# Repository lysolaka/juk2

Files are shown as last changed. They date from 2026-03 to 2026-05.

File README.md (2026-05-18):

# JUK2

JUK2 is a CNC plotter firmware for the ESP32-S3 on a custom PCB and plotter frame.

JUK2 is the successor of JUK - a private, messy and ugly project. The project's second version is supposed to be everything the first one was not able to be.

See the file `REFERENCE.md` for usage information.

# Hardware

The custom design can be found under the `juk-pcb` directory. It also has a schematic and a STEP model available for those, who don't have KiCad installed.

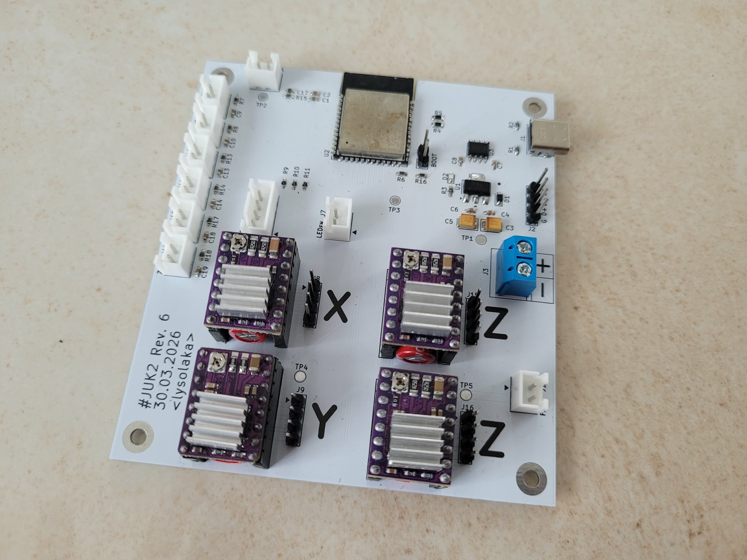
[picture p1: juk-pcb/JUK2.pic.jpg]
juk2pcb


The machine operates in Cartesian coordinates using four motors: one for X and Y axes each, and two for the Z axis. The X axis is realized as a moving table, the Y axis is being moved up and down by the Z axis. The X and Y assemblies operate using a belt pulley, the Z axis moves the Y axis assembly using trapezoidal screws from both ends of the axis (hence the need for two motors).

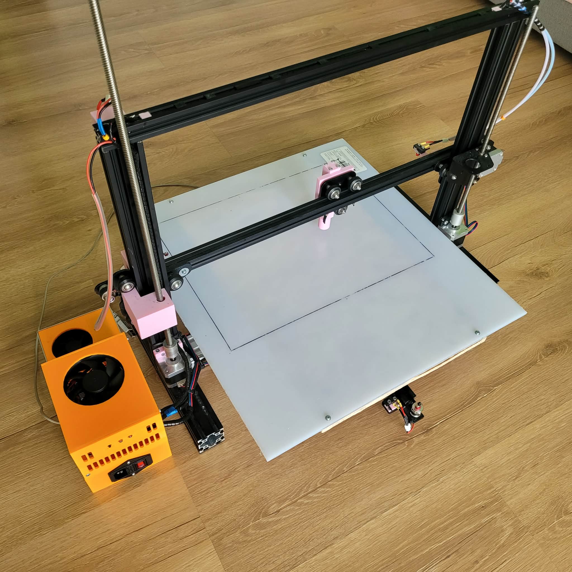
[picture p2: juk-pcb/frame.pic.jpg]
juk2frame


# Software

Just like the first edition of JUK, the entire software stack is developed using Rust. This time the project is split into crates in a single workspace. The structure is as follows:
- `juk-cmd`: command parsing and wire protocol library
- `juk-com`: a communication library implementing text and binary interfaces
- `juk-firmware`: the main firmware executable
- `juk-interp`: movement interpolators library
- `juk-led`: a simple library to use an RGB LED using PWM
- `juk-motion`: motion profiles library

## Toolchain

Building this project requires the Xtensa Rust Toolchain, detailed installation instructions can be found [here](https://docs.espressif.com/projects/rust/book/getting-started/toolchain.html). Additionaly the [espflash](https://github.com/esp-rs/espflash/tree/main/espflash) utility is needed to flash the program onto the board.

# License

All code and design files in this repository are licensed under the GPL-3 license.

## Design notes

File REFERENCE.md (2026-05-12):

# JUK2 - Reference

# Configuration Options

## Summary

| Option | Data Type | Values | Default Value |
|---|---|---|---|
| `accel`  | `f32` | \[`0.0`, `100000.0`\] | *TODO* |
| `frame`  | `enum` | `rel`, `abs` | `rel` |
| `led` | `u32` | \[`000000`, `ffffff`\]  | `00ff00` |
| `limits` | `[bool; 6]` | key is read-only | *undefined* |
| `mmpsX`  | `f32` | \(`0.0`, `1.0`\] | `0.0125625` |
| `mmpsY`  | `f32` | \(`0.0`, `1.0`\] | `0.0125625` |
| `mmpsZ`  | `f32` | \(`0.0`, `1.0`\] | *TODO* |
| `posX` | `i32` | \[`0`, `50000`\] | `0` |
| `posY` | `i32` | \[`0`, `50000`\] | `0` |
| `posZ` | `i32` | \[`0`, `50000`\] | `0` |
| `unit` | `enum` | `steps`, `mm` | `steps` |
| `vel` | `f32` | \[`0.0`, `50000.0`\] | *TODO* |

## Description

#### `accel` - Default Acceleration

Data type: `f32`
Value range: \[`0.0`, `100000.0`\]
Default value: *TODO*

Default acceleration value in `steps / s^2` used when the acceleration motion parameter is ommited.

Example:
```
set accel=12000.0
```

#### `frame` - Displacement Reference Frame

Data type: `enum`
Variants: `rel`, `abs`
Default value: `rel`

Reference frame to use when moving. `rel` means relative to the current position, `abs` - relative to the origin of the \[`posX`, `posY`, `posZ`\] vector.

Example:
```
set frame=abs
```

#### `led` - RGB LED Colour

Data type: `u32`
Value range: \[`000000`, `ffffff`\]
Default value: `00ff00`

RGB8 value in HTML notation.

Example:
```
set led=ff00ff
```

#### `limits` - Limit Switch Status

Data type: `[bool; 6]`
Default value: *undefined*

Limit switch status for each axis and each direction. The data type doesn't matter - the software will display the output in a friendly format.

This configuration key is read-only and cannot be used with the `set` command.

Example:
```
get limits
```

#### `mmps{X,Y,Z}` - Millimeters per Step Coefficient

Data type: `f32`
Value range: \(`0.0`, `1.0`\]
Default value:
- `mmps{X,Y}`: `0.0125625`
- `mmpsZ`: *TODO*

Millimeters per step coefficient for an axis. To make a move when the value of `unit` is `mm`, the displacement value is divided by its axis `mmps` value and rounded to the nearest integer.

Example:
```
set mmpsX=0.02
set mmpsY=0.0125
set mmpsZ=0.005
```

#### `pos{X,Y,Z}` - Current Position

Data type: `u32`
Value range: \[`0`, `50000`\]
Default value: `0`

Current position of the end-effector in the unit of steps. Each axis' value is set to 0 after homing that axis. Changing this value does not move the end-effector, it only changes the reference frame.

Example:
```
set posX=100
set posY=43
set posZ=0
```

#### `unit` - Displacement Units

Data type: `enum`
Variants: `steps`, `mm`
Default value: `steps`

Units to use for the displacement values. `steps` is in the unit of motor steps, `mm` is for millimeters.

Example:
```
set unit=mm
```

#### `vel` - Default Velocity

Data type: `f32`
Value range: \[`0.0`, `50000.0`\]
Default value: *TODO*

Default velocity value in `steps / s` used when the velocity motion parameter is ommited.

Example:
```
set vel=5000.0
```

# Interface

## Interface Modes

The interface can be in one of two states: text or binary. After reset the state is set to text, the user may communicate with the machine using a command line interface. Binary mode is used for communicating with a PC using messages in a binary format. To switch between the modes the user has to press `CTRL + Space` once or twice, depending on the current state of the input buffer. The user is also notified about the switch by a message on the terminal when said switch happens. The external RGB indicator colour shows the current mode: green means text mode, magenta - binary mode.

## Keybindings

While the interface is in text mode, the following key combinations are recognised:
- `?`: Displays help based on the current command, if the command name is not entered, displays the command list
- `CTRL + X`: Cancels the current movement and flushes the execution queue
- `CTRL + C`: Cancels the current input at the command line
- `CTRL + D`: If the command line is empty, issues a software reset
- `CTRL + Space`: Switch between text mode and binary mode
- `CTRL + G`: Easter egg

# Command Reference

## Arguments

Some commands have key-value arguments, they are given as:
```
<key>=<value>
```
where key names are strings. Values are parsed on a per-key basis: each key has their value requirements listed in its description.

## Displacement Arguments

Allowed values for displacement arguments depend on the current reference frame (config: `frame`) and the current unit (config: `unit`).

That is:
- `frame` = `rel`, `unit` = `steps`:
    - Data type: integer
    - Range: \[-50000, 50000\]

- `frame` = `rel`, `unit` = `mm`:
    - Data type: floating-point
    - Range: \[-500, 500\]

- `frame` = `abs`, `unit` = `steps`:
    - Data type: integer
    - Range: \[0, 50000\]

- `frame` = `abs`, `unit` = `mm`:
    - Data type: floating-point
    - Range: \[0, 5000\]

## Motion Arguments

Allowed values for acceleration and velocity arguments depend on the current unit (config: `unit`).

- `unit` = `steps`
    - Data type: floating-point
    - Range: 
        - acceleration: \[0, 100000\]
        - velocity: \[0, 50000\]

- `unit` = `mm`
    - Data type: floating-point
    - Range: the values must be non-negative and after conversion to steps, must fit into the range for `unit` = `steps`.

The acceleration is given as unit per second squared, velocity as unit per second.

## Argument Relations

If a command has required arguments, their description has an argument relation statement.

Let an imaginary command have argument keys:
- `foo`
- `bar`
- `baz`

The following list shows relation statements and their meaning (if a key is missing it is optional)

- `foo`, `bar`, `baz` are required:
```
* ( foo bar baz )
```

- At least one of `foo`, `bar`, `baz`:
```
|| ( foo bar baz )
```

- Exactly one of `foo`, `bar`, `baz`:
```
^^ ( foo bar baz )
```

## Commands List

#### `move` - Move in a Line

Examples:
```
move x=120 y=-400
move x=40.0 y=60.0 z=0.0
move x=1250 a=12000 v=8000
move x=-100.0 z=50.0 a=0
```

**Keys:**
- `x`: X axis displacement.
- `y`: Y axis displacement.
- `z`: Z axis displacement.
- `a`: Movement acceleration.
- `v`: Movement velocity.

**Relation:**
```
|| ( x y z )
```

#### `arc` - Move in an Arc

Examples:
```
arc x=-100 y=100 r=100 dir=pos
arc x=20.0 y=10.0 r=40.0 dir=neg
arc x=120 y=80 r=240 a=0 v=50
arc x=-10.0 y=-10.0 r=10.0 dir=neg a=500.0 v=100.0
```

**Keys:**
- `x`: X axis displacement.
- `y`: Y axis displacement.
- `z`: Z axis displacement. The arc is done in the XY plane. Use this to achieve helical motion.
- `r`: Arc radius. Adheres to the same rules as displacement, but must not be negative.
- `dir`: direction of the arc. `pos` means the direction where the angle of the radius vector increases, `neg` - where the angle decreases. Allowed values: `pos`, `neg`. Default is: `pos`
- `a`: Movement acceleration.
- `v`: Movement velocity.

**Relation:**
```
* ( x y r )
```

#### `home` - Perform Homing

Examples:
```
home
home axis=x
home axis=zy
home axis=xyz
```

**Keys:**
- `axis`: the axis (axes) to perform homing on. The only axes are `x`, `y`, `z`, so any combination of these three may be used. Default is: `xyz`.

#### `set` - Alter the configuration

Examples:
```
set unit=mm
set mmpsX=0.0125 posX=0 posY=500
```

**Keys:**

*see the configuration reference for the list of keys and their description*

**Relation:**
```
|| ( <keys> )
```

#### `get` - View the configuration

Examples:
```
get posX
get frame
get status
```

This commands functions differently than the others, namely the keys do not accept a value. This means that the following is an error:
```
get pos=loremipsum
```

**Keys:**

*see the configuration reference for the list of keys and their description*

Additionally the following keys are available:
- `pos`: absolute position of every axis in steps
- `mmps`: millimeters per step coefficient for every axis
- `status`: combined `pos`, `frame`, `unit` and limit switch information
- `version`: version information
- `license`: license information

**Relation:**
```
^^ ( <keys> )
```

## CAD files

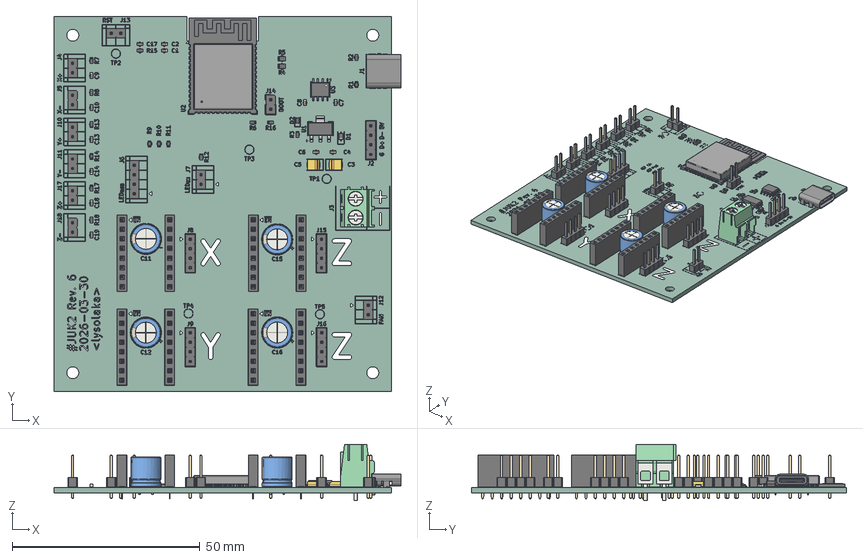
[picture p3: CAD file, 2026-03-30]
juk-pcb/JUK2.step
92.5 x 100.0 x 15.0 mm
PinHeader_1x02_P2.54mm_Vertical x 10
PinHeader_1x04_P2.54mm_Vertical x 6
R_0603_1608Metric x 16
C_0603_1608Metric x 13
PinSocket_1x08_P2.54mm_Vertical x 8
CP_Radial_D8.0mm_P3.50mm x 4
ESP32-S3-WROOM-1
D_SOD-323
TerminalBlock_Phoenix_PT-1,5-2-5.0-H_1x02_P5.00mm_Horizontal
R_0805_2012Metric x 2
JEITA_SOIC-8_3.9x4.9mm_P1.27mm
SOT-223
D_0603_1608Metric
CP_EIA-3528-15_AVX-H x 2
USB_C_Receptacle_GCT_USB4085
JUK2_silkscreen
JUK2_PCB

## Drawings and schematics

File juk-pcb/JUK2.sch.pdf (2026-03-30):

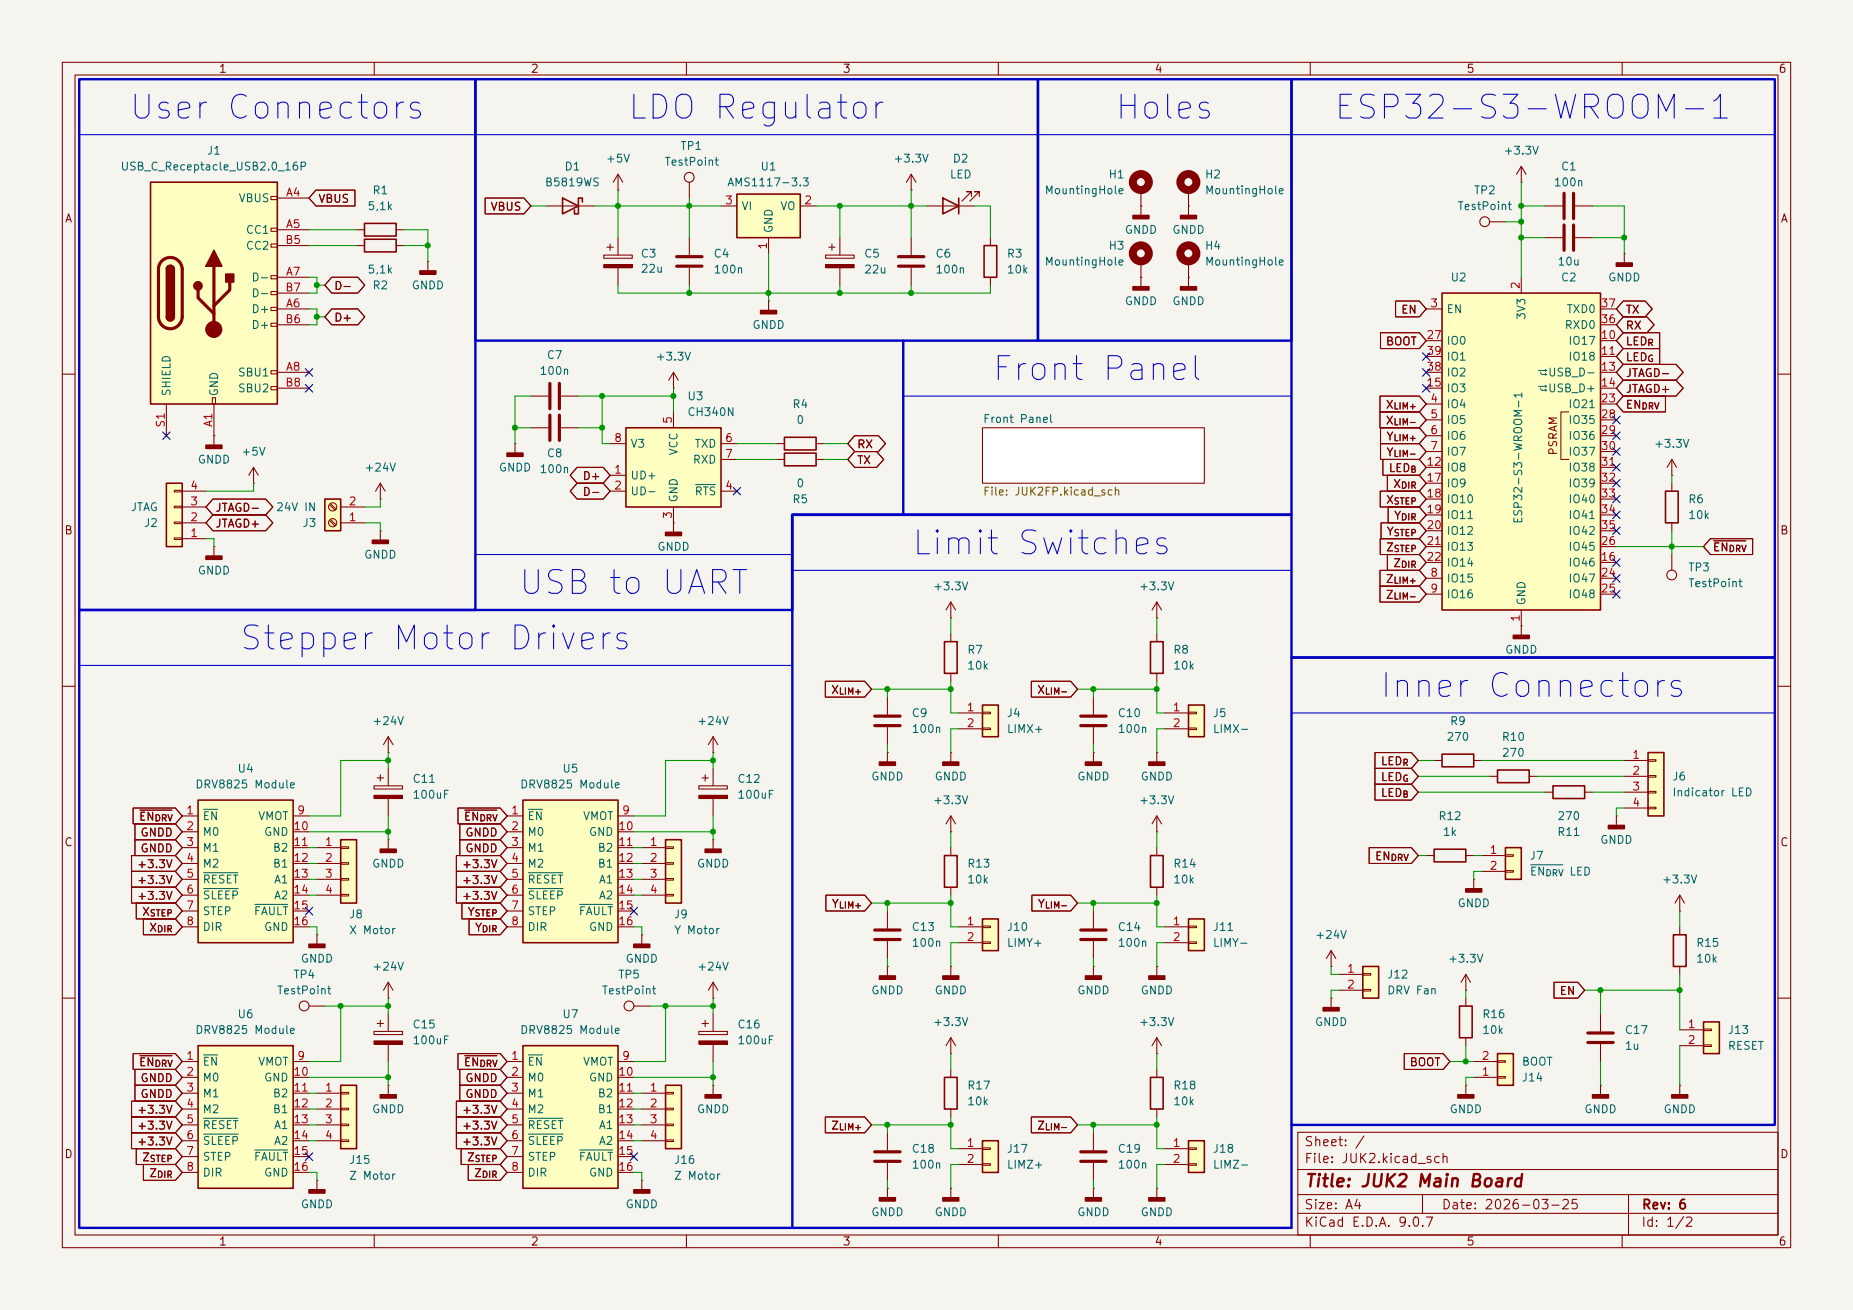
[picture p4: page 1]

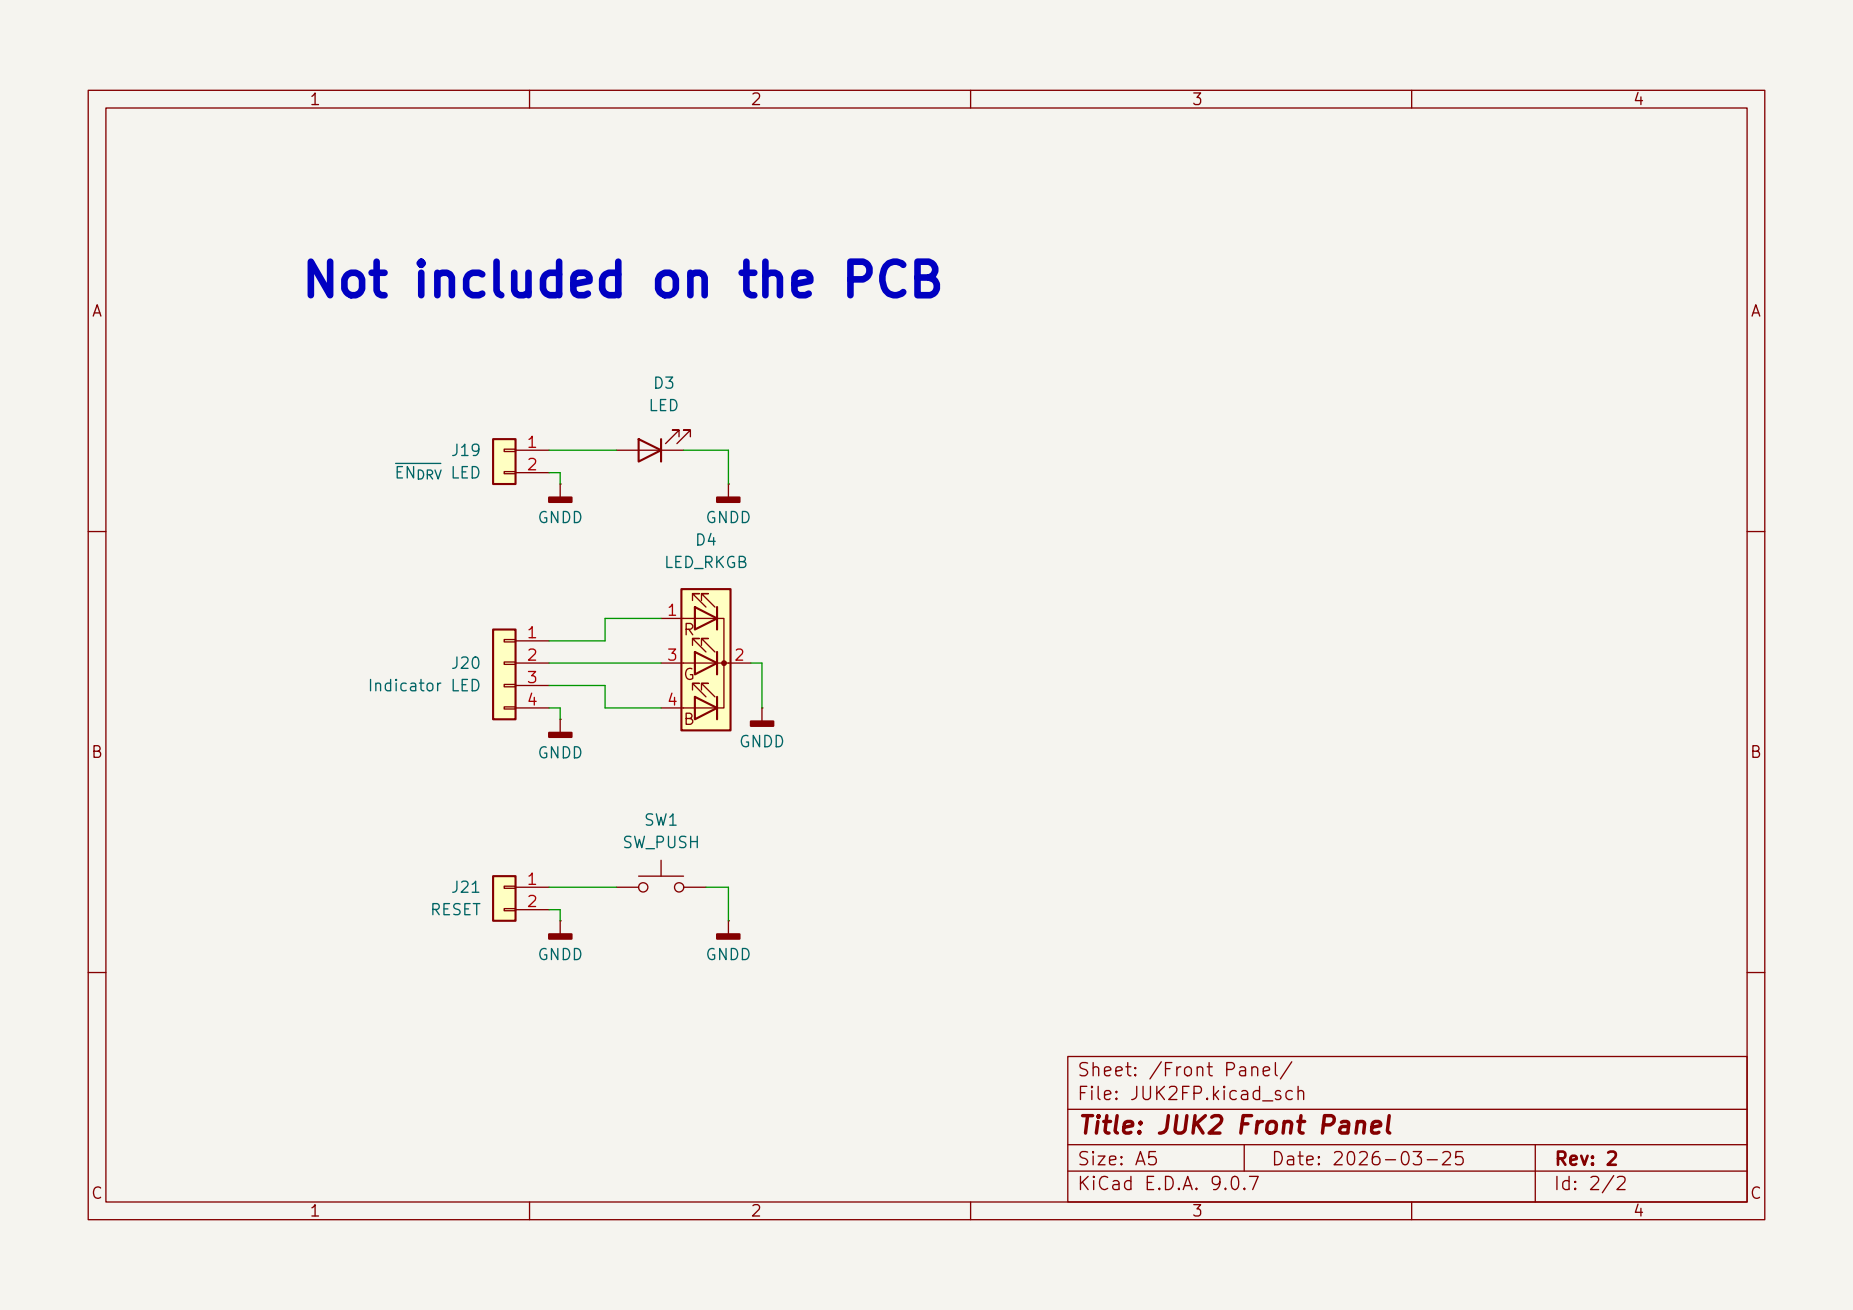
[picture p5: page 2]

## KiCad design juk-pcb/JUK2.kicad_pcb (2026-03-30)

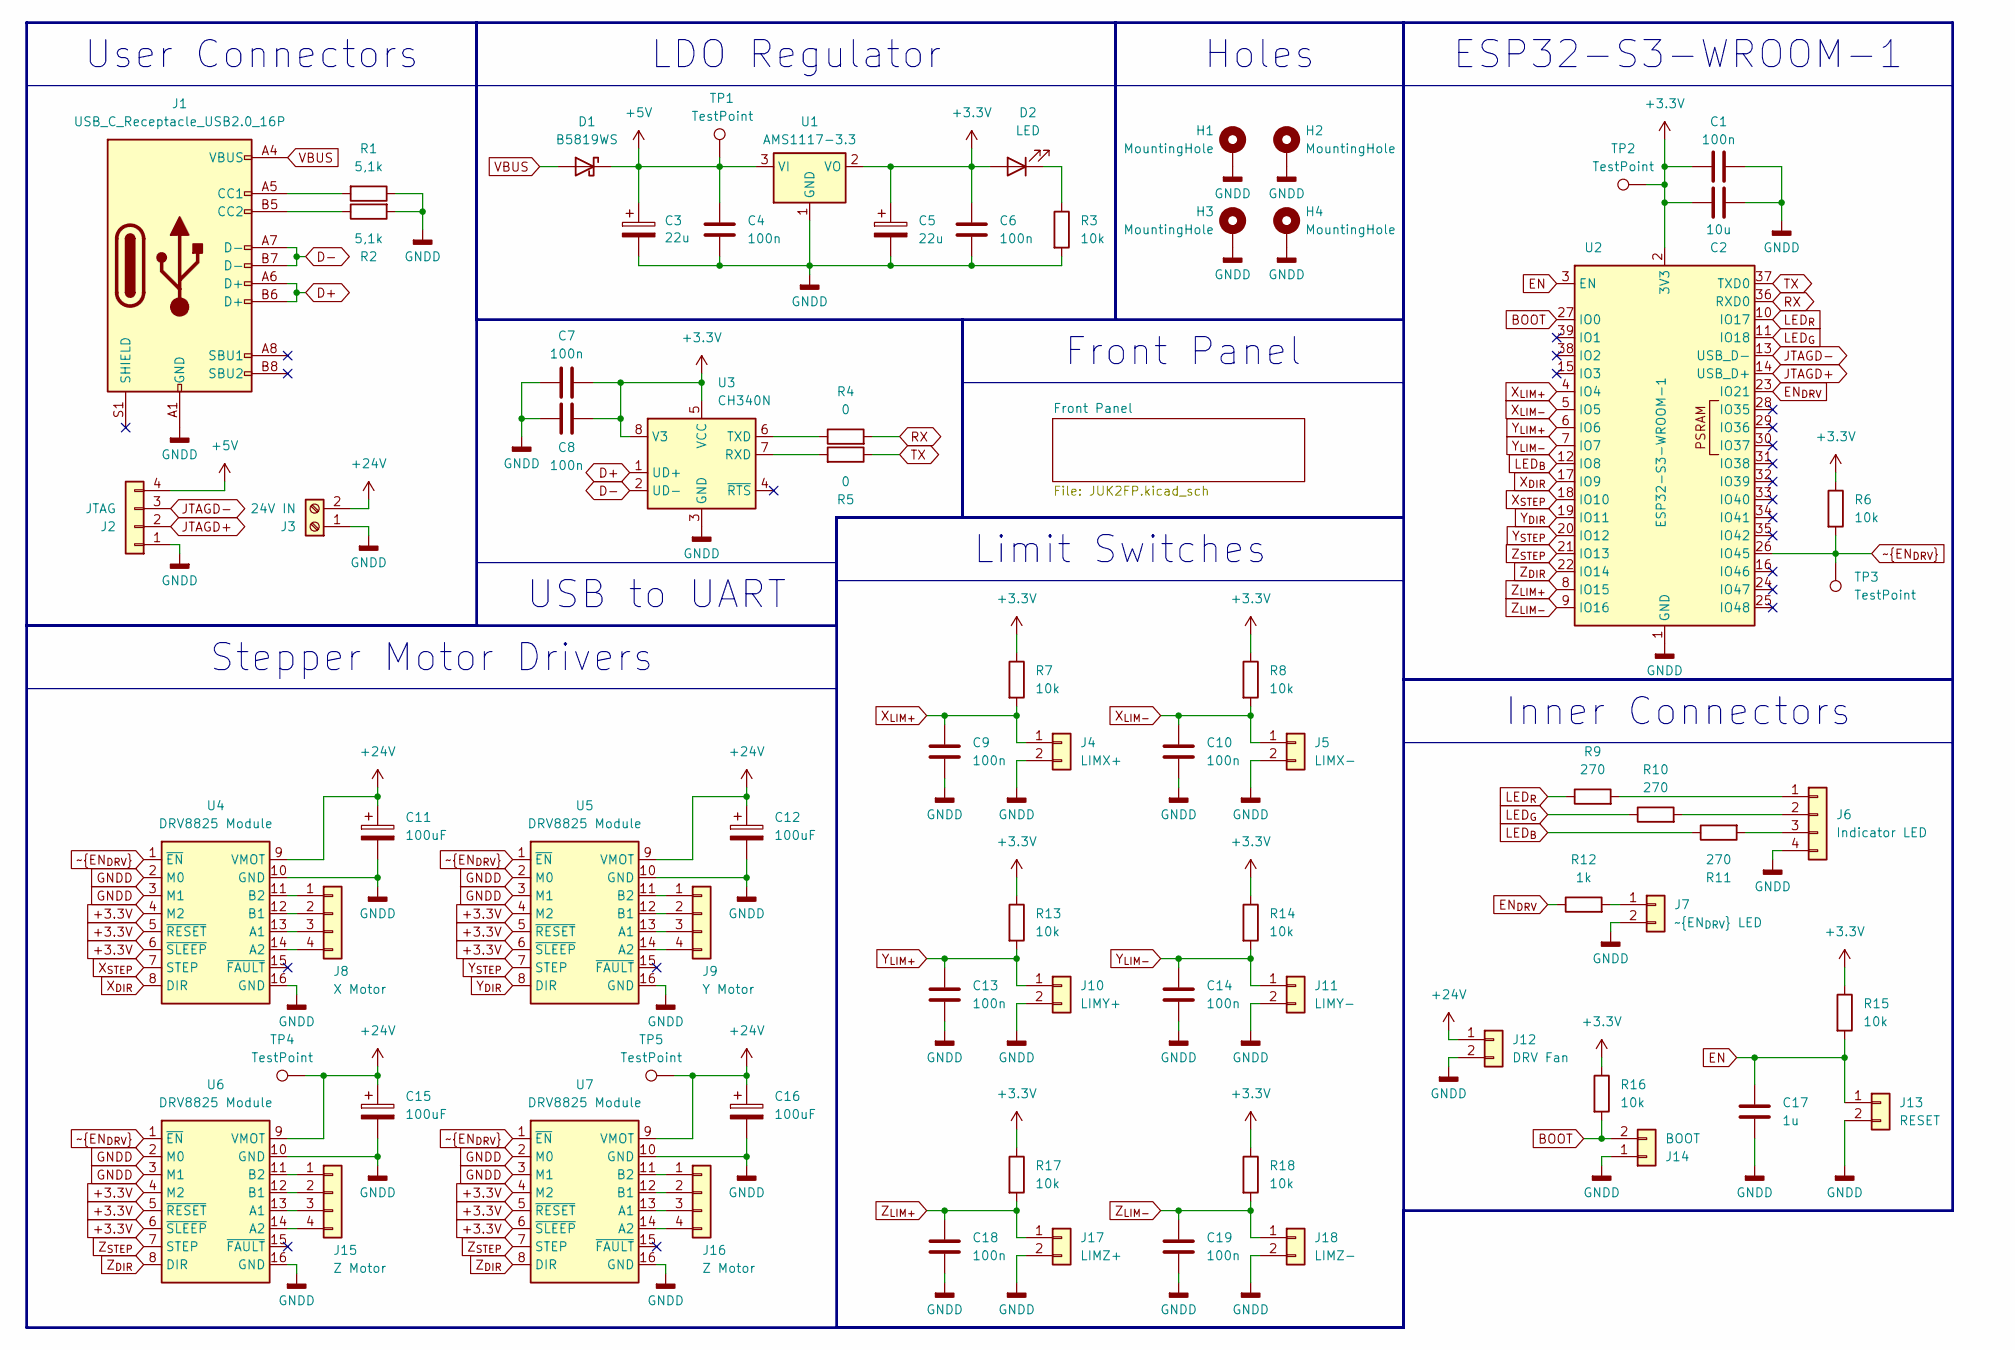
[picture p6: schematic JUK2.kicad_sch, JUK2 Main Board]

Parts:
C1, C4, C6, C7, C8, C9, C10, C13, C14, C18, C19: 100n; C_0603_1608Metric_Pad1.08x0.95mm_HandSolder
C2: 10u; C_0603_1608Metric_Pad1.08x0.95mm_HandSolder
C3, C5: 22u; CP_EIA-3528-15_AVX-H_HandSolder
C11, C12, C15, C16: 100uF; CP_Radial_D8.0mm_P3.50mm
C17: 1u; C_0603_1608Metric_Pad1.08x0.95mm_HandSolder
D1: B5819WS; D_SOD-323_HandSoldering
D2: LED; D_0603_1608Metric_Pad1.05x0.95mm_HandSolder
H1, H2, H3, H4: MountingHole; MountingHole_3.2mm_M3_Pad
J1: USB_C_Receptacle_USB2.0_16P; USB_C_GCT_USB4085
J2: JTAG; JTAGConnector
J3: 24V IN; TerminalBlock
J4: LIMX+; 2PinConnector
J5: LIMX-; 2PinConnector
J6: Indicator LED; 4PinConnector
J7: ~{EN_{DRV}} LED; 2PinConnector
J8: X Motor; MotorConnector
J9: Y Motor; MotorConnector
J10: LIMY+; 2PinConnector
J11: LIMY-; 2PinConnector
J12: DRV Fan; 2PinConnector
J13: RESET; 2PinConnector
J14: BOOT; PinHeader_1x02_P2.54mm_Vertical
J15, J16: Z Motor; MotorConnector
J17: LIMZ+; 2PinConnector
J18: LIMZ-; 2PinConnector
R1, R2: 5,1k; R_0603_1608Metric_Pad0.98x0.95mm_HandSolder
R3, R6, R7, R8, R13, R14, R15, R16, R17, R18: 10k; R_0603_1608Metric_Pad0.98x0.95mm_HandSolder
R4, R5: 0; R_0805_2012Metric_Pad1.20x1.40mm_HandSolder
R9, R10, R11: 270; R_0603_1608Metric_Pad0.98x0.95mm_HandSolder
R12: 1k; R_0603_1608Metric_Pad0.98x0.95mm_HandSolder
TP1, TP2, TP3, TP4, TP5: TestPoint; TestPoint_Pad_D2.0mm
U1: AMS1117-3.3; SOT-223-3_TabPin2
U2: ESP32-S3-WROOM-1
U3: CH340N; JEITA_SOIC-8_3.9x4.9mm_P1.27mm
U4, U5, U6, U7: DRV8825 Module; DRV8825_Module

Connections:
+3.3V: C1.1, C2.2, C5.1, C6.1, C7.2, C8.2, D2.2 (A), R6.1, R7.1, R8.1, R13.1, R14.1, R15.1, R16.1, R17.1, R18.1, TP2.1, U1.2 (VO), U2.2 (3V3), U3.5 (VCC), U3.8 (V3), U4.4 (M2), U4.5 (~RESET), U4.6 (~SLEEP), U5.4 (M2), U5.5 (~RESET), U5.6 (~SLEEP), U6.4 (M2), U6.5 (~RESET), U6.6 (~SLEEP), U7.4 (M2), U7.5 (~RESET), U7.6 (~SLEEP)
+5V: C3.1, C4.1, D1.1 (K), J2.4, TP1.1, U1.3 (VI)
+24V: C11.1, C12.1, C15.1, C16.1, J3.2, J12.1, TP4.1, TP5.1, U4.9 (VMOT), U5.9 (VMOT), U6.9 (VMOT), U7.9 (VMOT)
BOOT: J14.2, R16.2, U2.27 (IO0)
D+: J1.A6 (D+), J1.B6 (D+), U3.1 (UD+)
D-: J1.A7 (D-), J1.B7 (D-), U3.2 (UD-)
EN: C17.1, J13.1, R15.2, U2.3 (EN)
EN_{DRV}: R12.1, U2.23 (IO21)
GNDD: C1.2, C2.1, C3.2, C4.2, C5.2, C6.2, C7.1, C8.1, C9.2, C10.2, C11.2, C12.2, C13.2, C14.2, C15.2, C16.2, C17.2, C18.2, C19.2, H1.1, H2.1, H3.1, H4.1, J1.A1 (GND), J1.A12 (GND), J1.B1 (GND), J1.B12 (GND), J2.1, J3.1, J4.2, J5.2, J6.4, J7.2, J10.2, J11.2, J12.2, J13.2, J14.1, J17.2, J18.2, R1.1, R2.2, R3.2, U1.1 (GND), U2.1 (GND), U2.40 (GND), U2.41 (GND), U3.3 (GND), U4.2 (M0), U4.3 (M1), U4.10 (GND), U4.16 (GND), U5.2 (M0), U5.3 (M1), U5.10 (GND), U5.16 (GND), U6.2 (M0), U6.3 (M1), U6.10 (GND), U6.16 (GND), U7.2 (M0), U7.3 (M1), U7.10 (GND), U7.16 (GND)
JTAGD+: J2.2, U2.14 (USB_D+)
JTAGD-: J2.3, U2.13 (USB_D-)
LED_{B}: R11.1, U2.12 (IO8)
LED_{G}: R10.1, U2.11 (IO18)
LED_{R}: R9.1, U2.10 (IO17)
unnamed: D2.1 (K), R3.1
unnamed: J1.A5 (CC1), R1.2
unnamed: J1.B5 (CC2), R2.1
unnamed: J6.1, R9.2
unnamed: J6.2, R10.2
unnamed: J6.3, R11.2
unnamed: J7.1, R12.2
unnamed: J8.1, U4.11 (B2)
unnamed: J8.2, U4.12 (B1)
unnamed: J8.3, U4.13 (A1)
unnamed: J8.4, U4.14 (A2)
unnamed: J9.1, U5.11 (B2)
unnamed: J9.2, U5.12 (B1)
unnamed: J9.3, U5.13 (A1)
unnamed: J9.4, U5.14 (A2)
unnamed: J15.1, U6.11 (B2)
unnamed: J15.2, U6.12 (B1)
unnamed: J15.3, U6.13 (A1)
unnamed: J15.4, U6.14 (A2)
unnamed: J16.1, U7.11 (B2)
unnamed: J16.2, U7.12 (B1)
unnamed: J16.3, U7.13 (A1)
unnamed: J16.4, U7.14 (A2)
unnamed: R5.2, U3.7 (RXD)
unnamed: R4.1, U3.6 (TXD)
RX: R4.2, U2.36 (RXD0)
TX: R5.1, U2.37 (TXD0)
VBUS: D1.2 (A), J1.A4 (VBUS), J1.A9 (VBUS), J1.B4 (VBUS), J1.B9 (VBUS)
X_{DIR}: U2.17 (IO9), U4.8 (DIR)
X_{LIM+}: C9.1, J4.1, R7.2, U2.4 (IO4)
X_{LIM-}: C10.1, J5.1, R8.2, U2.5 (IO5)
X_{STEP}: U2.18 (IO10), U4.7 (STEP)
Y_{DIR}: U2.19 (IO11), U5.8 (DIR)
Y_{LIM+}: C13.1, J10.1, R13.2, U2.6 (IO6)
Y_{LIM-}: C14.1, J11.1, R14.2, U2.7 (IO7)
Y_{STEP}: U2.20 (IO12), U5.7 (STEP)
Z_{DIR}: U2.22 (IO14), U6.8 (DIR), U7.8 (DIR)
Z_{LIM+}: C18.1, J17.1, R17.2, U2.8 (IO15)
Z_{LIM-}: C19.1, J18.1, R18.2, U2.9 (IO16)
Z_{STEP}: U2.21 (IO13), U6.7 (STEP), U7.7 (STEP)
~EN_{DRV}: R6.2, TP3.1, U2.26 (IO45), U4.1 (~EN), U5.1 (~EN), U6.1 (~EN), U7.1 (~EN)

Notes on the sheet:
ESP32-S3-WROOM-1
Limit Switches
Front Panel
LDO Regulator
Holes
Inner Connectors
USB to UART
Stepper Motor Drivers
User Connectors

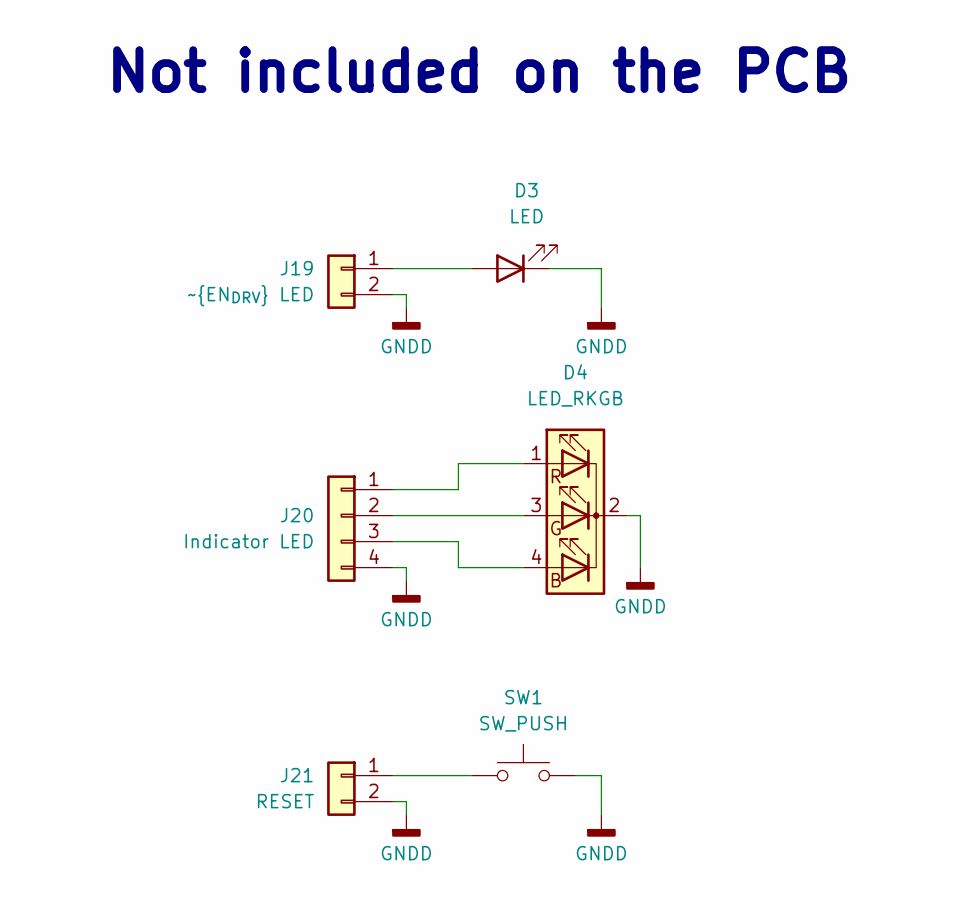
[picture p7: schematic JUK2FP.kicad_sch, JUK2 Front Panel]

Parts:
D3: LED; LED_D5.0mm
D4: LED_RKGB; LED_D5.0mm-4_RKGB
J19: ~{EN_{DRV}} LED; 2PinConnector
J20: Indicator LED; 4PinConnector
J21: RESET; 2PinConnector
SW1: SW_PUSH; SW_PUSH_6mm_H13mm

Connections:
unnamed: D3.1 (K), D4.2 (K), J19.2, J20.4, J21.2, SW1.2
unnamed: D3.2 (A), J19.1
unnamed: D4.1 (RA), J20.1
unnamed: D4.3 (GA), J20.2
unnamed: D4.4 (BA), J20.3
unnamed: J21.1, SW1.1

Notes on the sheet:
Not included on the PCB

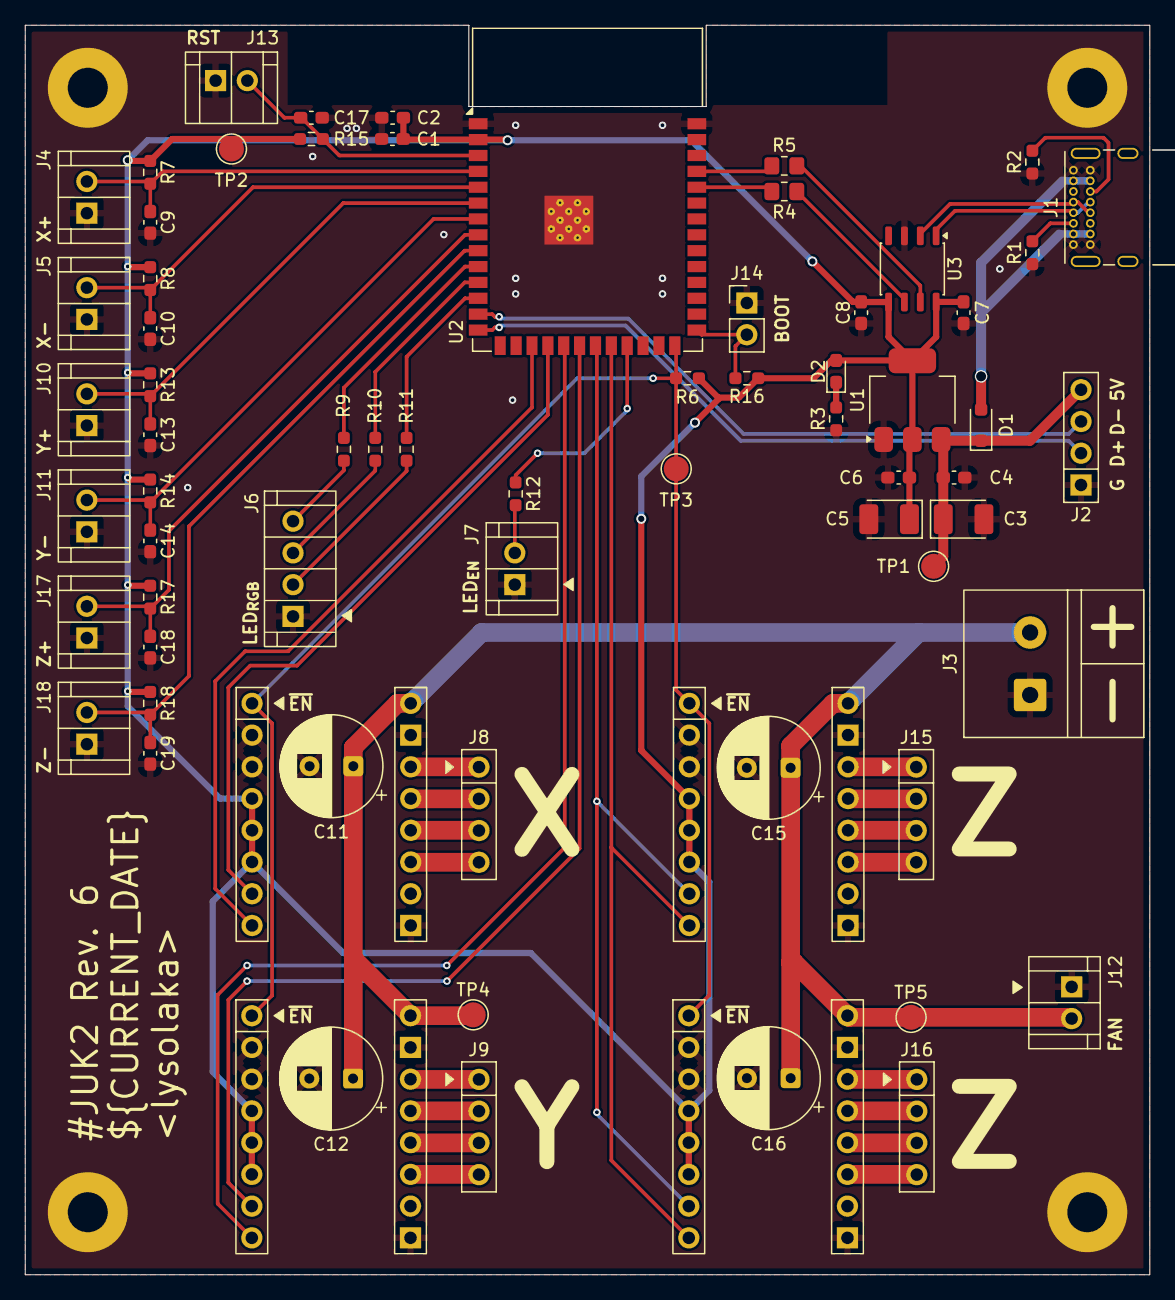
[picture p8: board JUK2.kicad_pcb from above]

Board: 2 copper layers, 90.0 x 100.0 mm, 73 parts (0 on the bottom side), 55 nets.

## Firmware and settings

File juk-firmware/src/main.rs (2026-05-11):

#![no_std]
#![no_main]
#![deny(
    clippy::mem_forget,
    reason = "mem::forget is generally not safe to do with esp_hal types, especially those \
    holding buffers for the duration of a data transfer."
)]

extern crate alloc;

use esp_hal::{
    interrupt::software::SoftwareInterruptControl,
    system::Stack,
    timer::systimer::SystemTimer,
};

use esp_rtos::embassy::Executor;

use esp_backtrace as _;
use esp_println as _;

use static_cell::{ConstStaticCell, StaticCell};

use juk_firmware::{app_core, main_core};

/// Main core executor
static MAIN_EXECUTOR: StaticCell<Executor> = StaticCell::new();
/// Application core stack (128K)
static APP_STACK: ConstStaticCell<Stack<131072>> = ConstStaticCell::new(Stack::new());
/// Application core executor
static APP_EXECUTOR: StaticCell<Executor> = StaticCell::new();

esp_bootloader_esp_idf::esp_app_desc!();

esp_hal::assign_resources! {
    Resources<'d> {
        com: ComResources<'d> {
            uart: UART0,
        },
        led: LedResources<'d> {
            r: GPIO17,
            g: GPIO18,
            b: GPIO8,
            ctrl: LEDC,
        },
        limits: LimitsResources<'d> {
            io: IO_MUX,
            x_p: GPIO4,
            x_m: GPIO5,
            y_p: GPIO6,
            y_m: GPIO7,
            z_p: GPIO15,
            z_m: GPIO16,
        },
        motor: MotorResources<'d> {
            tim: TIMG0,
            en_drv: GPIO45,
            en_led: GPIO21,
            x_step: GPIO10,
            x_dir: GPIO9,
            y_step: GPIO12,
            y_dir: GPIO11,
            z_step: GPIO13,
            z_dir: GPIO14,
        },
    }
}

#[esp_hal::main]
fn main() -> ! {
    // we configure the clocks and etc. here to avoid doing it later
    // the default config is the best config
    let config = esp_hal::Config::default();
    let peripherals = esp_hal::init(config);

    // see `lib.rs` for why this is such a pain
    let resources = split_resources!(peripherals);
    let resources = juk_firmware::Resources {
        com: juk_firmware::ComResources {
            uart: resources.com.uart,
        },
        led: juk_firmware::LedResources {
            r: resources.led.r,
            g: resources.led.g,
            b: resources.led.b,
            ctrl: resources.led.ctrl,
        },
        limits: juk_firmware::LimitsResources {
            io: resources.limits.io,
            x_p: resources.limits.x_p,
            x_m: resources.limits.x_m,
            y_p: resources.limits.y_p,
            y_m: resources.limits.y_m,
            z_p: resources.limits.z_p,
            z_m: resources.limits.z_m,
        },
        motor: juk_firmware::MotorResources {
            tim: resources.motor.tim,
            en_drv: resources.motor.en_drv,
            en_led: resources.motor.en_led,
            x_step: resources.motor.x_step,
            x_dir: resources.motor.x_dir,
            y_step: resources.motor.y_step,
            y_dir: resources.motor.y_dir,
            z_step: resources.motor.z_step,
            z_dir: resources.motor.z_dir,
        },
    };

    // turn on the heap allocator
    esp_alloc::psram_allocator!(peripherals.PSRAM, esp_hal::psram);

    // start the RTOS timer
    let SystemTimer { alarm0, .. } = SystemTimer::new(peripherals.SYSTIMER);
    esp_rtos::start(alarm0);

    // start the application core (still don't know why we need software interrupts for this)
    let SoftwareInterruptControl {
        software_interrupt0,
        software_interrupt1,
        ..
    } = SoftwareInterruptControl::new(peripherals.SW_INTERRUPT);
    esp_rtos::start_second_core(
        peripherals.CPU_CTRL,
        software_interrupt0,
        software_interrupt1,
        APP_STACK.take(),
        || {
            let app_executor = APP_EXECUTOR.init(Executor::new());
            app_executor.run(|spawner| {
                // spawn the main task for the application core, which gets the spawner and can control its thread
                spawner.must_spawn(app_core::main(spawner, resources.limits, resources.motor));
            })
        },
    );

    let main_executor = MAIN_EXECUTOR.init(Executor::new());
    main_executor.run(|spawner| {
        // spawn the main task for the main thread
        spawner.must_spawn(main_core::main(spawner, resources.com, resources.led));
    })
}

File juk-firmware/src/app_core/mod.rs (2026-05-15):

//! Code running on the second core (app core)

mod limits;
mod motor;

use alloc::{format, vec};

use embassy_executor::Spawner;
use embassy_futures::select::{Either, select};
use embassy_time::Timer;

use juk_cmd::{
    MotionError,
    cmd::{ArcDir, Axis, Command, Displacement, Response},
    config::InterfaceMode,
    defaults,
};
use juk_interp::{ArcGenerator, LineGenerator};
use juk_motion::{FastTrap, Flat, Profile};

use crate::{LimitsResources, MotorResources, global, strings};

#[embassy_executor::task]
pub async fn main(
    _spawner: Spawner, // no tasks on this core
    limits: LimitsResources<'static>,
    motor: MotorResources<'static>,
) -> ! {
    let mut motorctl = motor::init(motor);

    // wait for the stuff to settle
    Timer::after_millis(20).await;
    limits::init(limits);

    defmt::info!("Motor control unit started");

    loop {
        // execute the movement and get the result
        let res = match global::MOVEMENT.receive().await {
            Command::Move { x, y, z, a, v } => run_move(&mut motorctl, x, y, z, a, v).await,
            Command::Arc {
                x,
                y,
                z,
                r,
                dir,
                a,
                v,
            } => run_arc(&mut motorctl, x, y, z, r, dir, a, v).await,
            Command::Home { x, y, z } => run_homing(&mut motorctl, x, y, z).await,
            _ => defmt::unreachable!(),
        };

        // determine the interface mode so that we can format the message
        let interface_mode = {
            let c = global::SYSCFG.lock().await;
            c.mode
        };

        // format the message to send back to the interface
        let msg = match interface_mode {
            InterfaceMode::Binary => {
                // in binary mode we send stuff regardless what happens
                let ser = if let Err(e) = res {
                    defmt::error!("Movement error: {}", e);
                    postcard::to_allocvec_cobs(&Response::Err(e))
                } else {
                    postcard::to_allocvec_cobs(&Response::Ok)
                };

                match ser {
                    Ok(buf) => buf,
                    Err(e) => {
                        defmt::error!("Response serialization failed: {}", e);
                        // nuke the receiver
                        vec![b'\0', b'\0']
                    }
                }
            }
            InterfaceMode::Text => {
                // in text mode we only send messages on errors
                if let Err(e) = res {
                    defmt::error!("Movement error: {}", e);
                    format!("{}Cannot execute: {}\r\n", strings::ERROR, e).into_bytes()
                } else {
                    continue;
                }
            }
        };

        // send the message to the interface
        global::TERMINAL.send(msg).await;
    }
}

async fn run_move(
    ctl: &mut motor::MotorControl<'_>,
    x: Displacement,
    y: Displacement,
    z: Displacement,
    a: f32,
    v: f32,
) -> Result<(), MotionError> {
    // we can copy the position since we're not moving at this point in time
    let pos = critical_section::with(|cs| *global::POS.borrow_ref(cs));

    let dx = x.to_relative(Axis::X, pos);
    let dy = y.to_relative(Axis::Y, pos);
    let dz = z.to_relative(Axis::Z, pos);

    let line = LineGenerator::new(dx, dy, dz)?;

    defmt::debug!(
        "Begin line movement, dx: {=i32}, dy: {=i32}, dz: {=i32}",
        dx,
        dy,
        dz,
    );

    // no acceleration means the flat profile
    if a == 0.0 {
        let mut prof = Flat::new(v, line.len() as u32)?;
        ctl.execute(line.step_iter(), prof.delays()).await;
    } else {
        let mut prof = FastTrap::new(a, v, line.len() as u32)?;
        ctl.execute(line.step_iter(), prof.delays()).await;
    }

    defmt::debug!("Line movement done");

    Ok(())
}

async fn run_arc(
    ctl: &mut motor::MotorControl<'_>,
    x: Displacement,
    y: Displacement,
    z: Displacement,
    r: u32,
    dir: ArcDir,
    a: f32,
    v: f32,
) -> Result<(), MotionError> {
    // we can copy the position since we're not moving at this point in time
    let pos = critical_section::with(|cs| *global::POS.borrow_ref(cs));

    let dx = x.to_relative(Axis::X, pos);
    let dy = y.to_relative(Axis::Y, pos);
    let dz = z.to_relative(Axis::Z, pos);

    defmt::debug!(
        "Begin arc movement, dx: {=i32}, dy: {=i32}, dz: {=i32}, r: {=u32}, dir: {:?}",
        dx,
        dy,
        dz,
        r,
        dir
    );

    let arc = ArcGenerator::new(dx, dy, dz, r, dir)?;

    // no acceleration means the flat profile
    if a == 0.0 {
        let mut prof = Flat::new(v, arc.len() as u32)?;
        ctl.execute(arc.step_iter(), prof.delays()).await;
    } else {
        let mut prof = FastTrap::new(a, v, arc.len() as u32)?;
        ctl.execute(arc.step_iter(), prof.delays()).await;
    }

    defmt::debug!("Arc movement done");

    Ok(())
}

async fn run_homing(
    ctl: &mut motor::MotorControl<'_>,
    x: bool,
    y: bool,
    z: bool,
) -> Result<(), MotionError> {
    // clear any stale cancel signal
    global::CANCEL.reset();

    match select(run_homing_impl(ctl, x, y, z), global::CANCEL.wait()).await {
        Either::First(res) => res,
        Either::Second(_) => {
            defmt::warn!("Homing aborted: cancelled by the user");
            Ok(())
        }
    }
}
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

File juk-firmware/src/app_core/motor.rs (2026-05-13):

//! Motion executor
use core::{
    cell::RefCell,
    sync::atomic::{AtomicBool, Ordering},
};

use critical_section::Mutex;
use embassy_futures::select::{Either, Either3, select, select3};
use esp_hal::{
    Blocking,
    gpio::{Level, Output, OutputConfig},
    time::Duration,
    timer::{OneShotTimer, timg::TimerGroup},
};
use heapless::spsc::{Consumer, Producer, Queue};

use juk_interp::Step;

use crate::{MotorResources, global, global::LimitStatus};

/// Pin for moving the X axis
static X_STEP: Mutex<RefCell<Option<Output>>> = Mutex::new(RefCell::new(None));
/// Pin for moving the Y axis
static Y_STEP: Mutex<RefCell<Option<Output>>> = Mutex::new(RefCell::new(None));
/// Pin for moving the Z axis
static Z_STEP: Mutex<RefCell<Option<Output>>> = Mutex::new(RefCell::new(None));

/// Pin for setting the X axis direction
static X_DIR: Mutex<RefCell<Option<Output>>> = Mutex::new(RefCell::new(None));
/// Pin for setting the Y axis direction
static Y_DIR: Mutex<RefCell<Option<Output>>> = Mutex::new(RefCell::new(None));
/// Pin for setting the Z axis direction
static Z_DIR: Mutex<RefCell<Option<Output>>> = Mutex::new(RefCell::new(None));

/// Step producer and consumer queue
static STEP_PC: (
    Mutex<RefCell<Option<Producer<'_, StepEvent>>>>,
    Mutex<RefCell<Option<Consumer<'_, StepEvent>>>>,
) = {
    static mut Q: Queue<StepEvent, 8> = Queue::new();
    // SAFETY: `Q` is only accessible in this scope
    #[allow(static_mut_refs)]
    let (p, c) = unsafe { Q.split_const() };

    (
        Mutex::new(RefCell::new(Some(p))),
        Mutex::new(RefCell::new(Some(c))),
    )
};

/// Abort condition variable, used to flush the step queue and abort movement
static ABORT_COND: AtomicBool = AtomicBool::new(false);

/// Pin set timer
static STEP_SET_TIM: Mutex<RefCell<Option<OneShotTimer<'_, Blocking>>>> =
    Mutex::new(RefCell::new(None));
/// Pin reset timer
static STEP_RESET_TIM: Mutex<RefCell<Option<OneShotTimer<'_, Blocking>>>> =
    Mutex::new(RefCell::new(None));

pub fn init(res: MotorResources<'static>) -> MotorControl<'static> {
    // configure timers
    let timg = TimerGroup::new(res.tim);

    let mut set_tim = OneShotTimer::new(timg.timer0);
    set_tim.set_interrupt_handler(step_set);
    set_tim.listen();

    let mut reset_tim = OneShotTimer::new(timg.timer1);
    reset_tim.set_interrupt_handler(step_reset);
    reset_tim.listen();

    // configure GPIO
    let x_step = Output::new(res.x_step, Level::Low, OutputConfig::default());
    let y_step = Output::new(res.y_step, Level::Low, OutputConfig::default());
    let z_step = Output::new(res.z_step, Level::Low, OutputConfig::default());

    let x_dir = Output::new(res.x_dir, Level::Low, OutputConfig::default());
    let y_dir = Output::new(res.y_dir, Level::Low, OutputConfig::default());
    let z_dir = Output::new(res.z_dir, Level::Low, OutputConfig::default());

    // install the statics
    critical_section::with(|cs| {
        X_STEP.borrow_ref_mut(cs).replace(x_step);
        Y_STEP.borrow_ref_mut(cs).replace(y_step);
        Z_STEP.borrow_ref_mut(cs).replace(z_step);

        X_DIR.borrow_ref_mut(cs).replace(x_dir);
        Y_DIR.borrow_ref_mut(cs).replace(y_dir);
        Z_DIR.borrow_ref_mut(cs).replace(z_dir);

        STEP_SET_TIM.borrow_ref_mut(cs).replace(set_tim);
        STEP_RESET_TIM.borrow_ref_mut(cs).replace(reset_tim);
    });

    // get the producer side of the queue
    let prod = critical_section::with(|cs| STEP_PC.0.borrow_ref_mut(cs).take().unwrap());

    MotorControl {
        drv: Output::new(res.en_drv, Level::High, OutputConfig::default()),
        led: Output::new(res.en_led, Level::Low, OutputConfig::default()),
        step_queue: prod,
    }
}

pub struct MotorControl<'d> {
    /// Motor driver IC enable line, active low
    drv: Output<'d>,
    /// LED indicator for the enable line
    led: Output<'d>,
    step_queue: Producer<'static, StepEvent>,
}

impl<'d> MotorControl<'d> {
    /// Execute the step and delay sequence, but return when a limit switch is hit or the user
    /// cancels the operation
    pub async fn execute<SI, DI>(&mut self, step_iter: SI, delay_iter: DI)
    where
        SI: Iterator<Item = (Step, Step, Step)>,
        DI: Iterator<Item = f32>,
    {
        // reset the abort state
        ABORT_COND.store(false, Ordering::Release);
        // reset any stale cancel signals
        global::CANCEL.reset();
        global::LIMIT_CANCEL.reset();
        // enable the driver
        self.drv.set_low();
        self.led.set_high();
        match select3(
            self.execute_impl(step_iter, delay_iter),
            global::CANCEL.wait(),
            global::LIMIT_CANCEL.wait(),
        )
        .await
        {
            Either3::First(_) => defmt::info!("Movement complete"),
            Either3::Second(_) => {
                ABORT_COND.store(true, Ordering::Release);
                defmt::warn!("Movement aborted: cancelled by the user");
            }
            Either3::Third(_) => {
                ABORT_COND.store(true, Ordering::Release);
                defmt::error!("Movement aborted: hit a limit switch");
            }
        }
        self.drv.set_high();
        self.led.set_low();
    }

    /// Execute the step and delay sequence, but return when a limit switch is hit. This version of
    /// `execute()` is only suitable for the homing sequence.
    ///
    /// # Warning
    ///
    /// This function does not check for the user cancel signal, the caller is responsible for doing
    /// that.
    pub async fn execute_homing<SI, DI>(&mut self, step_iter: SI, delay_iter: DI)
    where
        SI: Iterator<Item = (Step, Step, Step)>,
        DI: Iterator<Item = f32>,
    {
        // reset the abort state
        ABORT_COND.store(false, Ordering::Release);
        // reset any stale cancel signal
        global::LIMIT_CANCEL.reset();
        // enable the driver
        self.drv.set_low();
        self.led.set_high();
        match select(
            self.execute_impl(step_iter, delay_iter),
            global::LIMIT_CANCEL.wait(),
        )
        .await
        {
            Either::First(_) => (),
            Either::Second(_) => {
                ABORT_COND.store(true, Ordering::Release);
            }
        }
        self.drv.set_high();
        self.led.set_low();
    }
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

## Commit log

2026-02-03 feat: implement a driver for the WS2812 LED
2026-02-09 feat: implement UART echo
2026-02-11 feat(juk-led): implement `LEDAdapter` in blocking mode
2026-02-11 docs(juk-led): write docs for the `juk-led` library
2026-02-11 fix(juk-com): exit the binary mode with an event to redraw the prompt
    [lib.rs]
2026-03-30 feat: add a PCB design to the project
    [JUK2.kicad_pcb, JUK2.kicad_sch, JUK2.step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]
2026-04-02 feat(juk-led): implement a new RGB LED adapter
2026-04-02 feat(juk-firmware): write an example for the LED adapter usage
2026-04-02 feat(juk-led): move logs to the debug level
2026-04-20 feat(juk-motion): add errors and their handling
    [lib.rs]
2026-05-03 feat(juk-firmware): implement the LED controller task
2026-05-06 feat: implement interface mode switch hook
2026-05-06 feat(juk-firmware): add some missing globals
    [com.rs]
2026-05-06 fix(juk-firmware): flush the queue on the cancel input
    [com.rs]
2026-05-10 feat(juk-firmware): implement limit switch handling
2026-05-11 feat(juk-firmware): implement homing execution
2026-05-12 fix: cleanup after replacing the shorted capacitor
2026-05-12 feat(juk-firmware): implement error handling for the movement executor
    [mod.rs]
2026-05-12 fix(juk-cmd): make homing fail for unknown values of `axis`
2026-05-13 fix(juk-firmware): adjust imports for the juk-interp move
    [mod.rs, motor.rs]
2026-05-13 fix: adjust code for the `juk-cmd` refactor
    [com.rs, lib.rs, mod.rs]
2026-05-13 fix(juk-cmd): export `ParseError` (used in `Displacement`)
    [lib.rs]
2026-05-13 fix(juk-firmware): make homing cancellable
    [mod.rs, motor.rs]
2026-05-15 fix: send async messages in binary mode
    [mod.rs]
2026-05-18 fix(juk-firmware): ignore no-op commands instead of failing
    [mod.rs]
2026-05-25 Revert "fix(juk-firmware): ignore no-op commands instead of failing"
    The error handling should be done by the user instead of making the code
    more complicated here.
    This reverts commit a1a5db336c381a9ed70433db7a8571d2cc6799b9.
    [mod.rs]
